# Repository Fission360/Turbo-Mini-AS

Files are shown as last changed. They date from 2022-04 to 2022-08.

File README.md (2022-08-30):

# Turbo-Mini-AS



I love my V0.1 very much. But with my current setup, the stock part cooling became the limiting factor in my quest for high-speed quality. This project was originally inspired by Vez3D and his cooling setup, and my design was built off of KurioHonoo's wonderful Mini AfterSherpa (https://github.com/KurioHonoo/Mini-AfterSherpa/blob/main/README.md).

If you're reading this, you are likely also be dissatisfied with the V0.1's part cooling performance. Enter Turbo Mini AfterSherpa.

# What is this thing?
The V0.1 is known to have a part-cooling bottleneck as parts are printed faster. This a mod that hopes to vastly improve your V0.1's part cooling performance, without compromising on the compact nature of the printer.

# Why would I want this over the stock fans?
 The 7040 brushelss blower fan provides a good amount of airflow to cool down parts, and is actually quieter than the stock 3010 blowers when ouputting the same volume of air. Also, for cooling-needy plastics like PLA and even PETG, the fan opens the door for higher printing speeds using these plastics.

# What hotends/extruders does this support?
Since this was based off the Mini AfterSherpa, this was built with the Sherpa Mini in mind. While the mounting is compatible with the Sailfin and Sharkfin, the duct may not be. There is a taller tube adapter for the Sherpa Micro if that's what you want, but you'll also need KurioHonoo's Sherpa Micro Adapter (https://github.com/KurioHonoo/Mini-AfterSherpa/blob/main/STL/Mini_AfterSherpa/MiniAS_Sherpa_Micro_Adapter.stl). I haven't tested that setup myself, so I can't guarantee that everything will fit as well as with the Sherpa Mini. 
 
Currently only Dragon/Dragonfly and Revo Voron hotends are supported. I don't have any plans to do an Orbiter V1.5/V2 version, and my design is extremely hard to modify to work with the Revo Micro.

# Can I get the CAD?
I only have the STEP posted; I will not be posting the Fusion 360 file publicly simply because the timeline is attrocious. If you want the F3D file, let me know.

If you have any other questions, I'm @where'sthelambSAUCE in the Voron discord server.

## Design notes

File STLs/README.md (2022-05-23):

# Note: while the fan shroud itself can be fitted onto any printer with the V0.1 x-carriage, the fan mount used in this mod is intended for use with a hinged tophat.
I decided that having the 7040 blower fan mounted to the tophat was the best option for a couple reasons. This prevented any electronics from needing to be moved and also didn't require you to cut any new panels (in an attempt to make this mod as accessible as possible). But this also means you can't fully remove the tophat, since it will stay connected due to the fans wires. Adding a hinged tophat made this problem trivial. If you do not plan on adding a hinged tophat, then you will need to create your own mounting solution. That being said, I would highly recommend the tophat made by MSiemons: https://github.com/VoronDesign/VoronUsers/tree/master/printer_mods/MSiemons/TophatHingeV0.1

# Print Settings
All of these parts will print comfortably within your V0.1's build volume. ABS/ASA is preferred for all of the parts, and I would honestly recommend using a brim at least for Turbo_Mini_AS.stl, since any warping can cause some fitment issues down the road.

Go ahead and use your normal Voron recommended settings for Turbo_Mini_AS.stl, but for everything else, I would change the inner and outer perimeters to 0.6mm

# STL Changelog
5/12/22: Updated the shroud with better duct paths and newer outlet direction, as well as adding general aesthetic tune-ups. It also uses less plastic than the previous version, helping remove some of the weight

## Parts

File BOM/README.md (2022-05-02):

# BOM
**Electronics**
  - Assembled Sherpa Mini (use an M3 bolt instead of a thumbscrew): https://github.com/Annex-Engineering/Sherpa_Mini-Extruder
  - CPAP tubing: https://www.amazon.com/SnugellTM-Universal-Premium-Compatible-Respironics/dp/B08C6XBCLY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
  - Blower fan (24V): https://www.aliexpress.com/item/32980201709.html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 OR https://www.aliexpress.com/item/4000959990877.html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
  - Low-pass filter
    - 1x 10K resistor (link for assorted kit): https://www.amazon.com/gp/product/B07L851T3V/ref=ppx_yo_dt_b_search_asin_title?ie=UTF8&psc=1
    - 1x 1uF capacitor (link for assorted kit): https://www.amazon.com/dp/B07KC99W2K?psc=1&ref=ppx_yo2ov_dt_b_product_details
    - 1x 1-pin female dupont connector (link for assorted kit): https://www.amazon.com/gp/product/B07CVYPDGS/ref=ppx_yo_dt_b_search_asin_title?ie=UTF8&psc=1
    - 1x 2.54mm JST-XH 2-pin and 1x 2.54mm JST-XH 3-pin (link for assorted kit): https://www.amazon.com/gp/product/B0731NHS9R/ref=ppx_yo_dt_b_search_asin_title?ie=UTF8&th=1
    - Wire
    - Solder and soldering iron

**Hardware**
  - 4x M3x5x4 threaded inserts: https://www.aliexpress.com/item/4000761483243.html?spm=a2g0o.order_list.0.0.7d741802ue7PZJ
  - 2x M3x8 screws (for mounting the Sherpa Mini to the shroud)
  - 2x M3x6 screws
  - 3x M2.5x12 screws
  - Double-sided tape
  - Electrical tape
  - Zipties

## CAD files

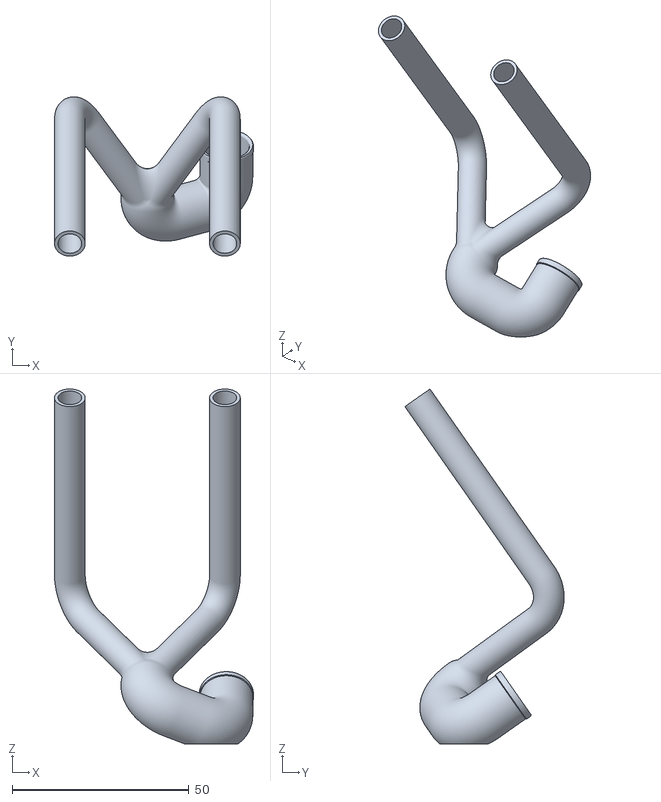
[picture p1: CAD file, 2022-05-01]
STLs/Sherpa_Micro_Tube_Adapter.stl
56.4 x 45.1 x 100.6

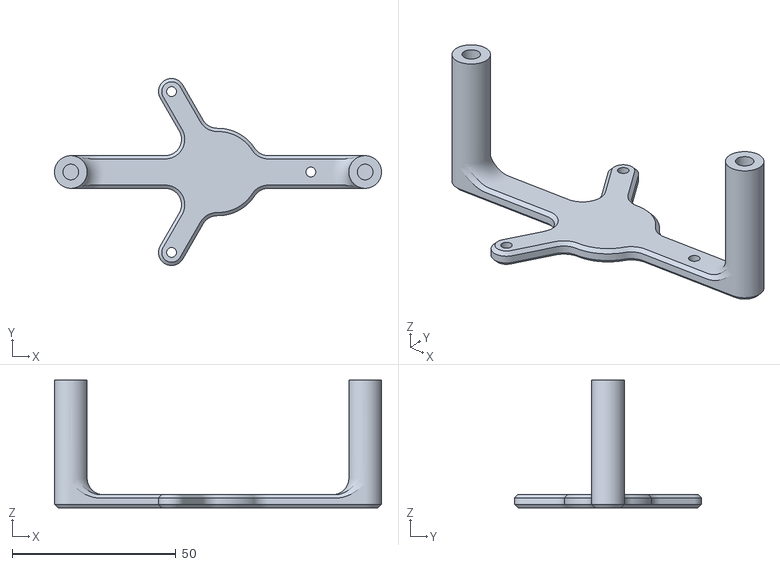
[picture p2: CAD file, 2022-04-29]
STLs/Fan Mount.stl
100.0 x 57.2 x 39.0

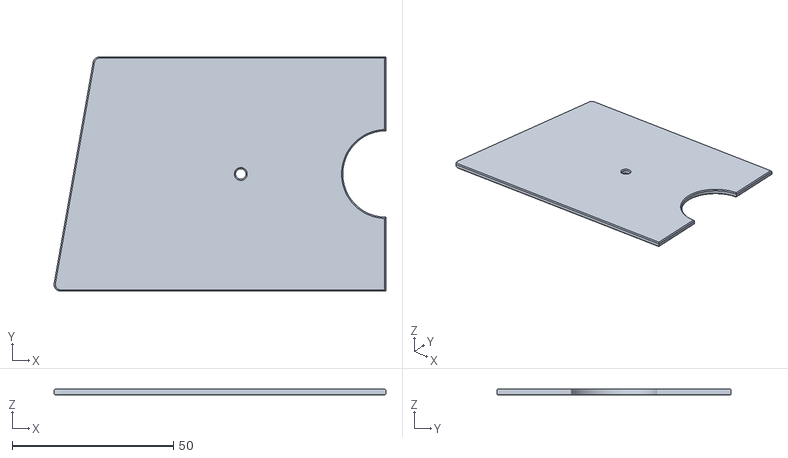
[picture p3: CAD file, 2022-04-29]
STLs/Tophat_Panel_2.stl
102.9 x 72.6 x 2.00

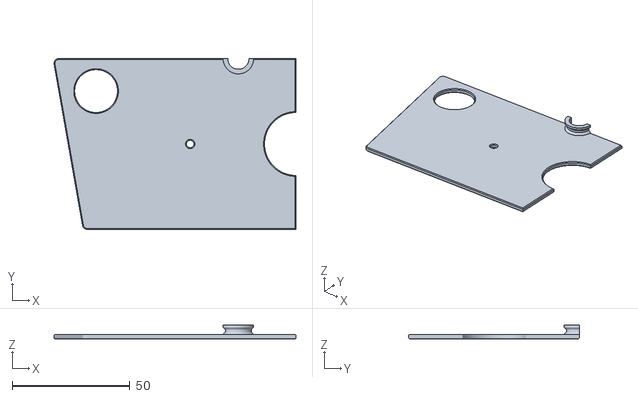
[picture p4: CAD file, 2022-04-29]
STLs/Tophat_Panel_1.stl
102.9 x 72.6 x 6.00

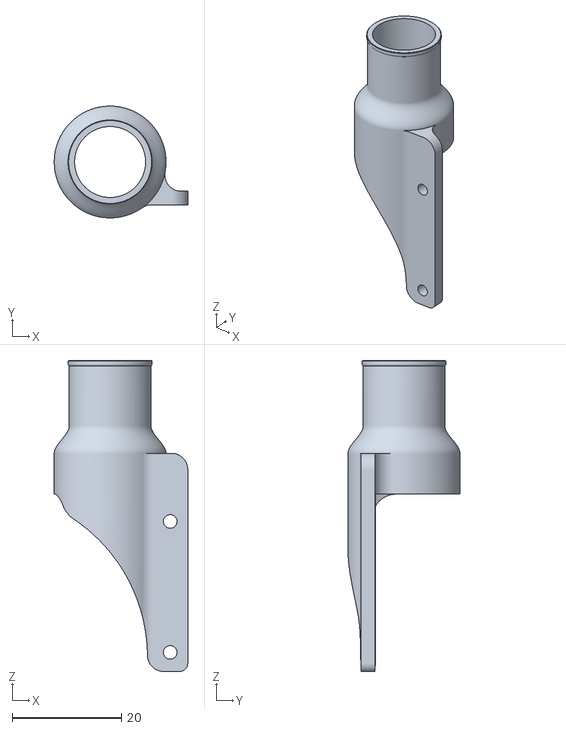
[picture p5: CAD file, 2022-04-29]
STLs/CPAP fan outlet adapter.stl
24.5 x 20.5 x 57.0

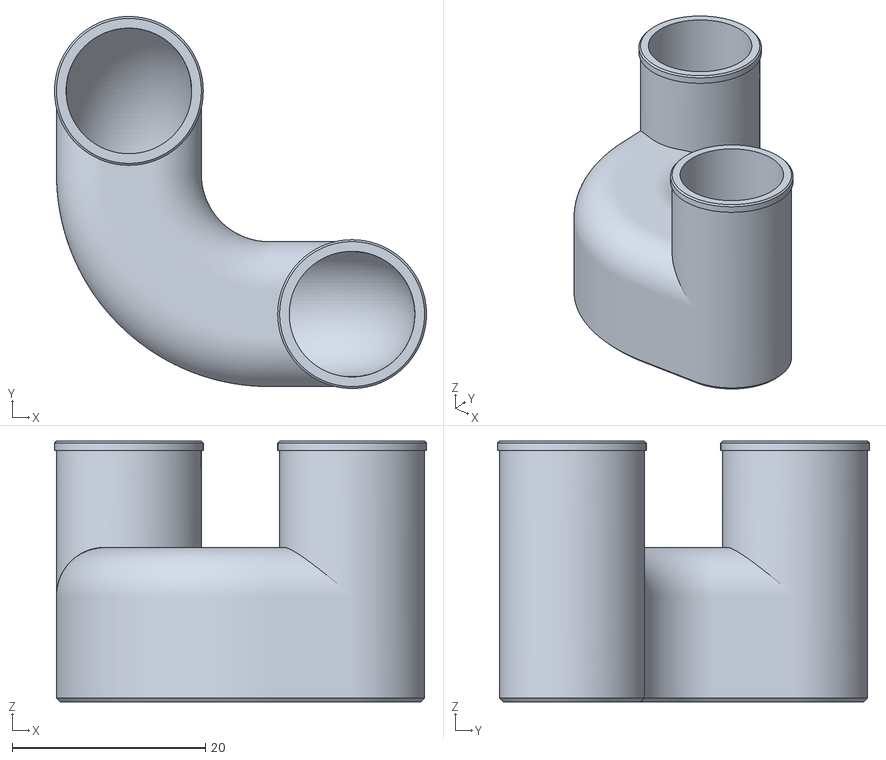
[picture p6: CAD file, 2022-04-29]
STLs/Hose Connector.stl
38.5 x 38.5 x 27.0

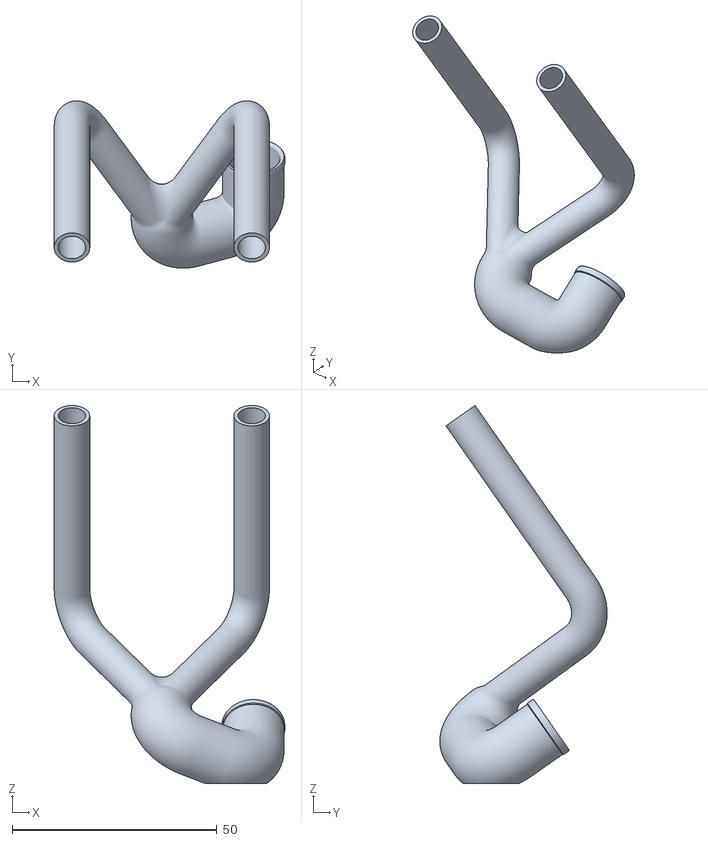
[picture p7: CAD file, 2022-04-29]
STLs/Tube_Adapter.stl
56.4 x 40.9 x 92.4

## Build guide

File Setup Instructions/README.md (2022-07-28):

# Print Your Parts
Firstly, you'll need to print out all your parts. Like the Mini-AfterSherpa, you'll need to press two threaded inserts into the top of the shroud, but you'll also need to press two inserts in to the posts of the fan mount. Set up your hotend as you did on your original one, ommitting the part cooling fans and mounting the Sherpa Mini to the top. The Dragonfly mounting holes are the original shorter ones, so they'll need M2.5x6 screws for mounting, but if you want that fixed, let me know.

# Mounting the Fan
First, you'll need to replace your back tophat panel with the two printed panel halves. Pretty self explanitory, just make sure the hole for the tube is on the left of the printer, when looking from the back. Take your three M2.5x12 screws and screw them from the back of the mount and into the posts on the fan. Then, mount the fan to the panel with two M3x6 screws. Run the wires under the small slot in the bottom of the panel and zip tie them from the inside. Finally, route the fan's connector and wires through the motor panel with the boweden tube and everything, leaving some slack to allow for the opening and closing of the tophat. It should look something like this when you're done:




# Hook Up the Tubing
You'll need two lengths of CPAP for this step, one ≈31cm long (we'll call it tube 1) and the other ≈28cm long (this will be tube 2). Tube 1 will connect the hotend tube adapter to the hose connector, and tube 2 will connect the hose connector to the CPAP fan outlet adapter on the fan. The hose connector will be mounted in front of the opening in the motor panel with double-sided tape (I wouldn't recommend using VHB tape here; it will be a pain in the butt to remove should you need to take off the motor panel). In order for the tube to bend in the correct way, you'll need to twist one end of each tube on the connector, so that the tube moves in the desired fashion. Add some electrical tape to the smaller ends of the fan outled adapter, so that you get a snug fit into the shroud. Final result will look like this:





# Wiring
Before you do anything else, I would highly recommend that you watch this video from Vez3D; it has a lot of information that helped me through my own build: https://www.youtube.com/watch?v=E3kBau82SwU
The below image is pulled from it.



I do have two differences when compared to his wiring. Firstly, in addition to having the grey wire connect to GPIO26, I also connect the black wire on the fan controller to a ground pin on my MCU (in my case an SKR Mini E3 V2). Secondly, In order to get a good signal from my control pin, I needed to put a low-pass filter between my fan's controller and my RPi and MCU. Shoutout to @ademuri on the Voron discord for the idea.



In this circuit diagram of a low-pass filter, the top wire is connecting GPIO26 to the fan controller, and the bottom wire is connecting your MCU ground to the fan controller. The input (left side in diagram) should be connected to your Pi and MCU, while the output (right side in diagram) should be connected to your fan controller. Wiring up the 10k resistor and the 1uF cap like the diagram will look similar to this:



Cover the resistor and cap leads with heatshrink, and add the connectors according to the finished wiring loom below. I took the 6-pin JST connector from the fan's included potentiometer, but used my own crimps on the wires:



Here it is fully wired up; the dupont connector goes to GPIO26, the 2-pin JST goes to any MCU port that connects to ground, and the 6-pin JST plugs back into the fan controller:



This solution works quite nicely, but as of right now, I'm only able to utilize around 66% of the blower's max available cooling power. This is because the fan's power from 0-100% is controlled by a voltage from 0-5V, while the Pi or MCU's control pin can only output 0-3.3V

I am looking into solution to fix this, but for now, this is the best solution I've been able to find, and I've still been happy with the results.

# Config/Klipper
I'm following Vez3D's example by controlling my printer via a pin on the Pi, so we need to set up the Pi as a second MCU for klipper to recognize the pin. (https://www.klipper3d.org/RPi_microcontroller.html). 

After you've followed those steps, in your config, you will need to change "fan" to the below settings and restart your firmware; I've found that for my particular setup, these settings allow me to go as low as 10-12% without the fan skipping.



Now you should be ready to print! Keep in mind that 100% fan is now wayyy stronger than before.

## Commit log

2022-04-29 Update and rename STLs.md to Print_Settings.md
2022-04-29 Rename Assembly Instructions/README.md to Setup Instructions/README.md
